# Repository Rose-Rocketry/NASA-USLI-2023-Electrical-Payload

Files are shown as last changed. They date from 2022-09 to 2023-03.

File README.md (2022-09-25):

# NASA-USLI-2023-Electrical-Payload

Welcome!

This repository is still in progress and houses the majority of the camera integration/functionality code for the NASA USLI 2023 Competition

Action items as of 9/25/2022:
- Add modular methods so other parts of the program can be run (i.e. "img2BW" "applySobel")
- Figure out how to do command line prompting to run the program so RF payload can use our program
- Prompt program to run with "[Radio Callsign] B2 A1 C3 D4 ..."
- Pick out and purchase microcontroller and antenna design
- Integrate camera to a microcontroller and upload code to microcontroller to run on boot (similar to systemctl)
- Have RF transmissions dictate the microcontroller operations of when to take pictures and apply filters (to be decided by RF Payload subsystem)
- Build antenna to send RF transmissions
- House camera payload in chassis to be determined by Mechanical Payload Team

Google Jamboard for Camera Payload: https://jamboard.google.com/d/17pDWzvR5QUZo6pmwbOdQxkDinwWt7RJfm15y4S94SMs/viewer?f=0

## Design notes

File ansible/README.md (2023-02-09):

# Local testing with vagrant
> Note: we should try to aim to make this as similar to the real thing as possible, but there's a limit to what we can test without the actual hardware

1. Install vagrant and ansible
> Note: If running on windows, make sure [Hyper-V](https://learn.microsoft.com/en-us/virtualization/hyper-v-on-windows/quick-start/enable-hyper-v) is enabled. This will require admin privliges in the terminal you expect to be working in as a limitation to Hyper-V.
2. Run `vagrant up`
> Note: Rose-Hulman blocks all DNS traffic that isn't to their dns servers, which breaks vagrant. This can be fixed by manually editing `/etc/resolv.conf` with `vagrant ssh`
3. After making changes to the ansible files, run `vagrant provision` to re-apply them. Run `vagrant destroy -f` to delete the VM's, and `vagrant up` to create new ones

# Flight Computer Setup Instructions
0. Required software: Raspberry Pi Imager, ansible
1. Flash "Raspberry Pi OS Lite (32 bit)" to the sd card with the Raspberry Pi Imager. Change the following settings:
```
[X] Set Hotname: rocket-pi
[X] Enable SSH
    [X] Password
    [ ] Public Key
[X] Set username and password
    Username: pi
```
> Note: We're gonna switch to 64-bit when we get the new pi's
2. Copying `wpa_supplicant.conf` from `boot` to the boot partition
> Note: If your using RHIT-OPEN, you must add the MAC address to clearpass before booting the pi
3. Eject the SD and boot the pi. This can take over 5 minutes!
4. Ensure you have ssh access with `ssh pi@rocket-pi`
> If you have a different hostname, be sure to update inventory.txt
5. Setup all of the software with `ansible-playbook playbook.yaml -i ansible_hosts` or `ansible-playbook playbook.yaml -i subscale_hosts` for subscale. This can also take a very long time

# IP Addresses
Withing the xblink network, all devices will be in the `10.82.104.0/24` subnet. The groundstation will have an ip of `10.82.104.2`, and rocket(s) will have ip(s) of `10.82.104.3`, `10.82.104.4`, etc...
> 82.104 is ASCII for `"Rh"`

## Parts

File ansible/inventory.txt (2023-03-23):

rocket-pi ansible_user=pi ansible_host=10.82.104.3 xb_device=/dev/ttyAMA0 xb_ip=10.82.104.3/24

[rocket]
rocket-pi

[pi]
rocket-pi

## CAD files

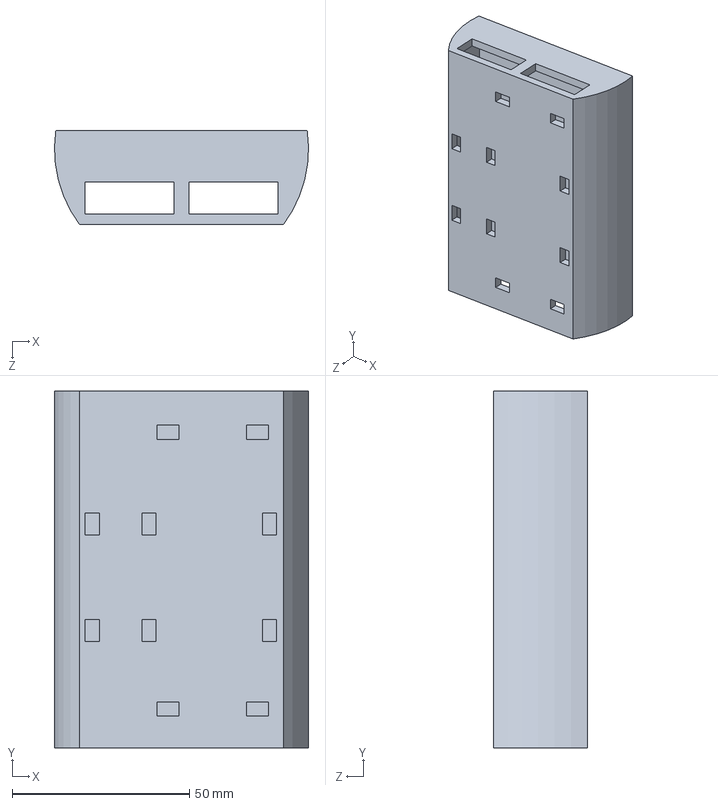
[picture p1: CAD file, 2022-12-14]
CAD/Subscale SDR Extension/Housing.SLDPRT
71.6 x 100.6 x 26.6 mm

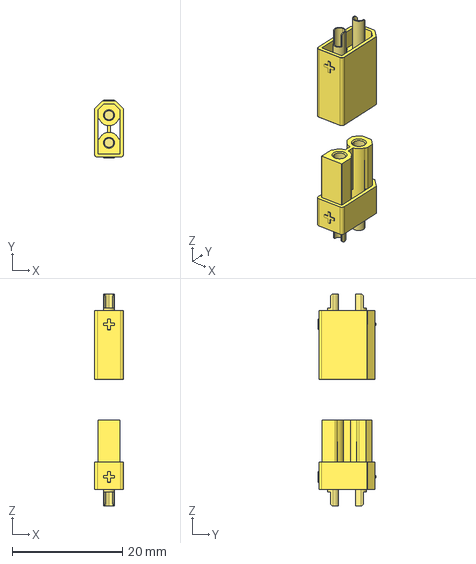
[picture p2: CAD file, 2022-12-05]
Motherboard/motherboard_2022_2023/3d_models/XT30U-M.step
5.25 x 10.4 x 38.5 mm

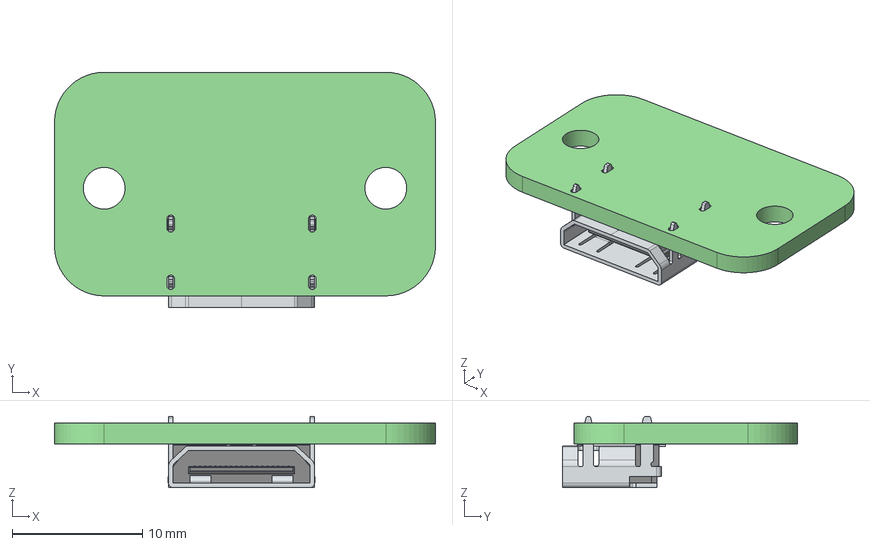
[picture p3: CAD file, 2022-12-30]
Motherboard/motherboard_2022_2023/hdmi_to_csi.step
29.2 x 18.1 x 5.45 mm
hdmi_to_csi PCB

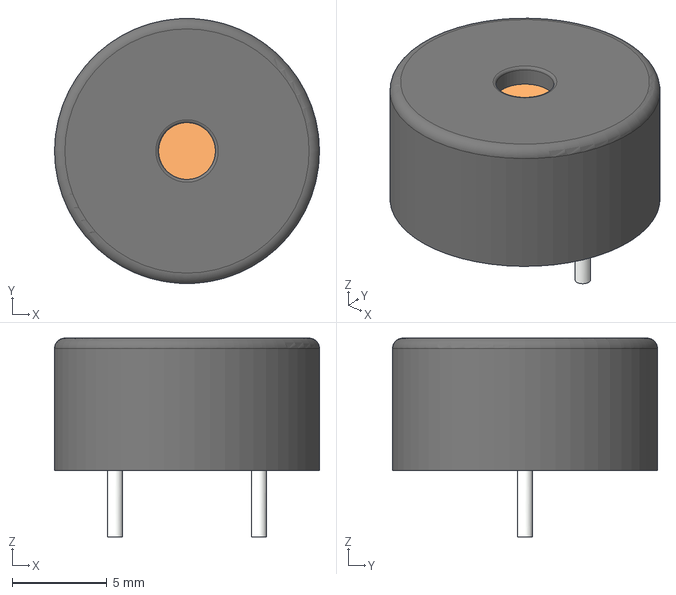
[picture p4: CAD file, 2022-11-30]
Motherboard/motherboard_2022_2023/3d_models/Piezo Buzzer.step
14.0 x 14.0 x 10.5 mm

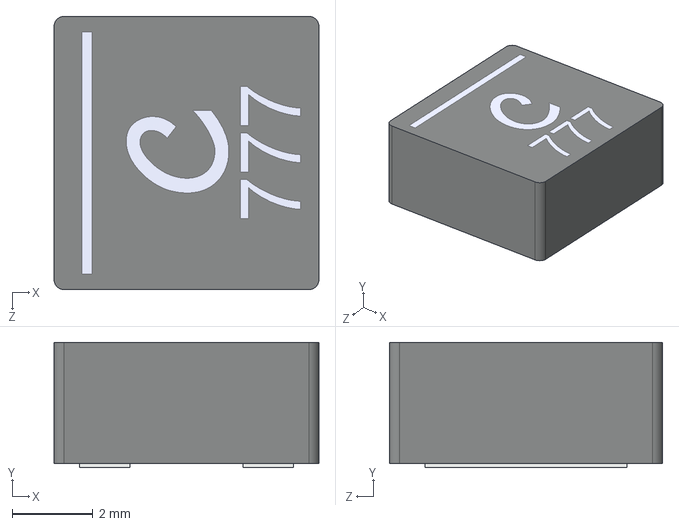
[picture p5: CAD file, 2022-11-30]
Motherboard/motherboard_2022_2023/3d_models/Coilcraft-XAL6030.step
6.56 x 3.10 x 6.76 mm

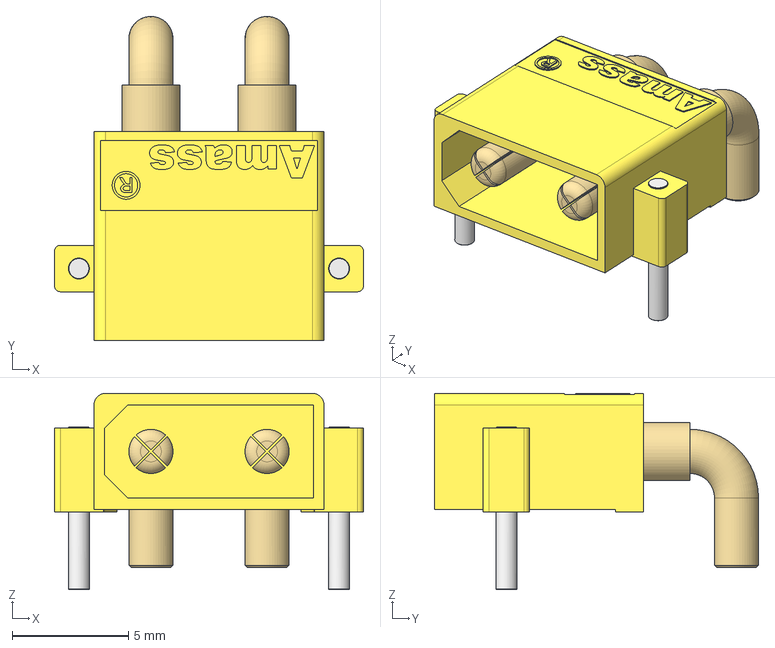
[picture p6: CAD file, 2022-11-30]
Motherboard/motherboard_2022_2023/3d_models/Amass_XT30PW-M.step
13.3 x 13.9 x 8.45 mm

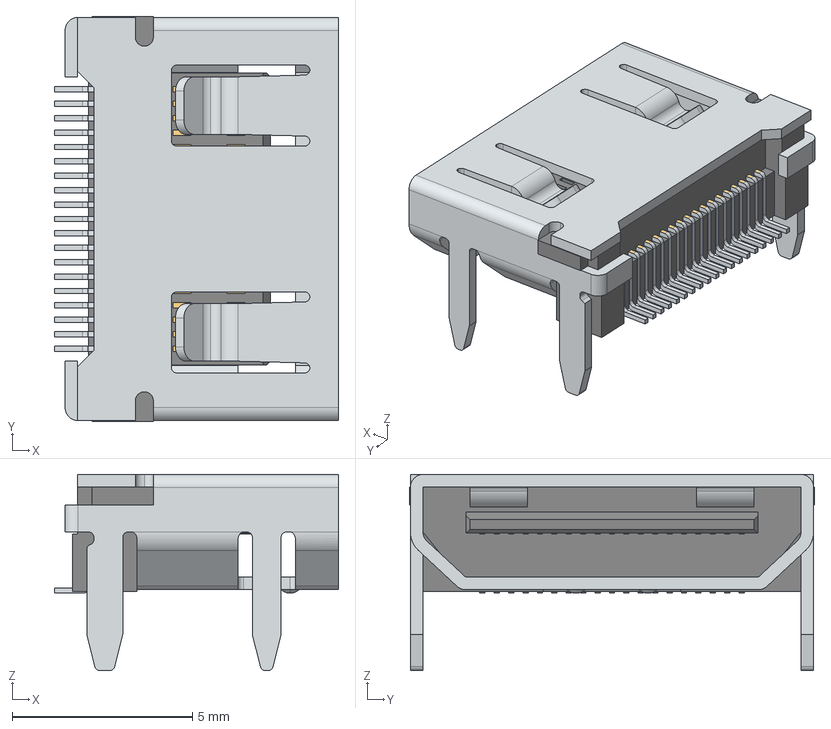
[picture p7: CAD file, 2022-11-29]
Motherboard/motherboard_2022_2023/3d_models/WURTH_685119136923.step
7.90 x 11.2 x 5.45 mm

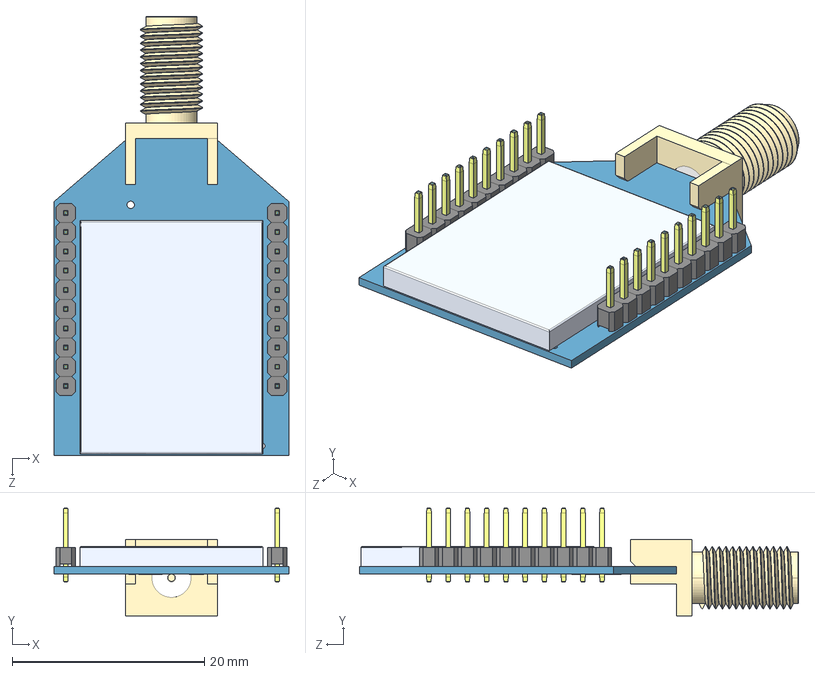
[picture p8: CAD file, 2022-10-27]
Motherboard/motherboard_2022_2023/3d_models/XBProRPSMA.step
24.4 x 11.2 x 45.6 mm
XBP24_board
2mmHeaderPin_straight x 20
XBPro_shield
RPSMA_XBee

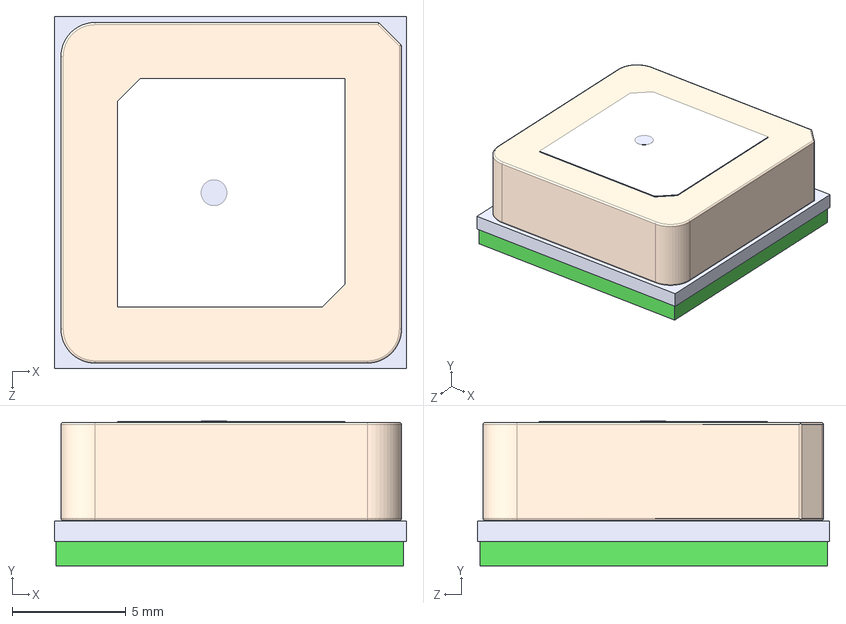
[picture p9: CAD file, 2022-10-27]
Motherboard/motherboard_2022_2023/3d_models/SAM_AP214.STEP
15.5 x 6.38 x 15.5 mm
Sam cavity
SAM PCB
SAM ANT

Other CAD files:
CAD/Subscale SDR Extension/Housing.STL

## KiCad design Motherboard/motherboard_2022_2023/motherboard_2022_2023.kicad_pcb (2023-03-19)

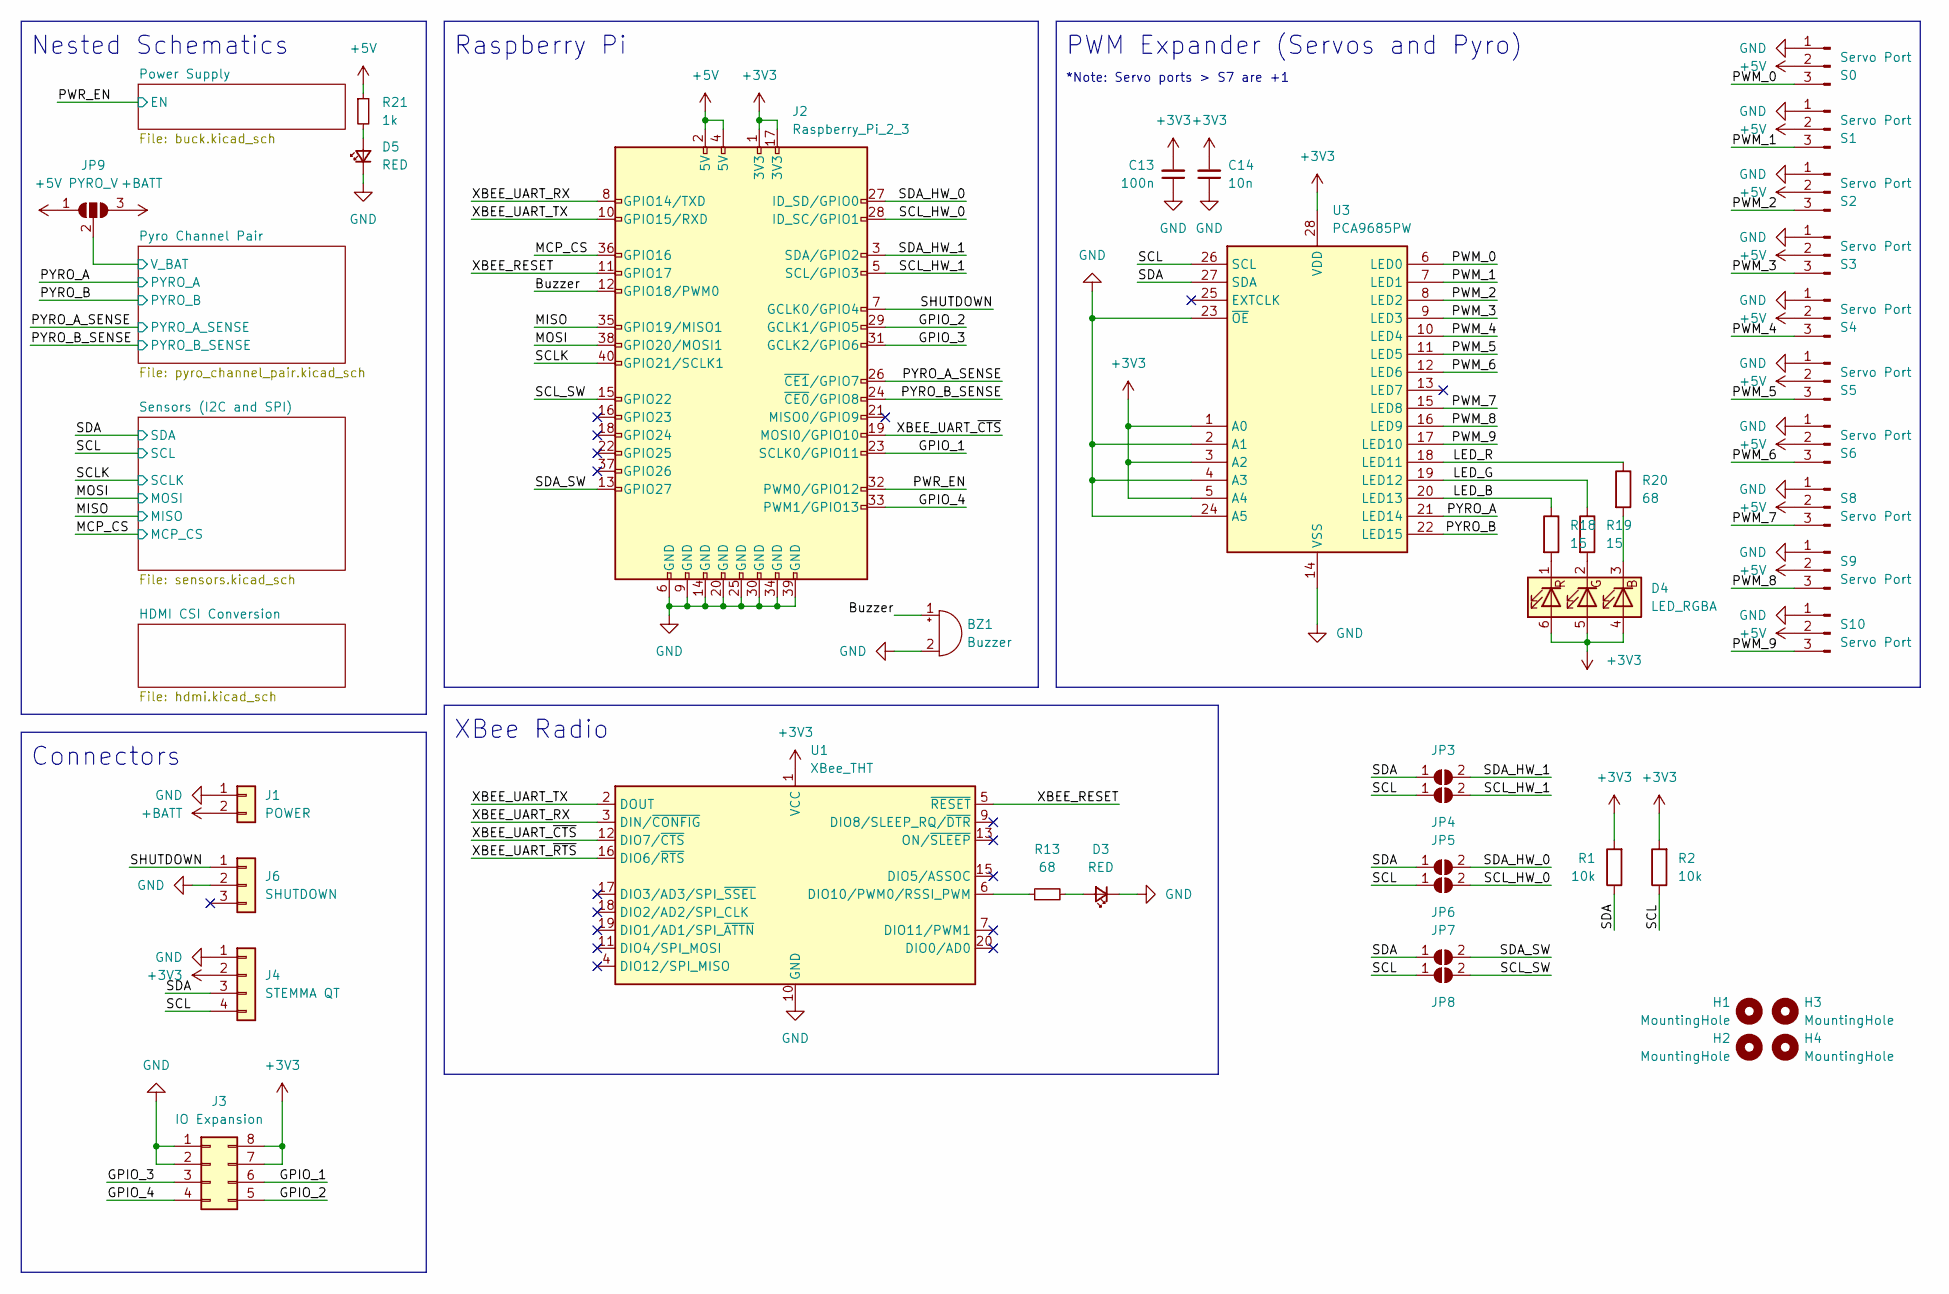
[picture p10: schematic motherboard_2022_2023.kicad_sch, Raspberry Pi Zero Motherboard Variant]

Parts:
BZ1: Buzzer; CPI-1375-80T
C13: 100n; C_0603_1608Metric
C14: 10n; C_0603_1608Metric
D3, D5: RED; LED_0603_1608Metric
D4: LED_RGBA; LED_RGB_5050-6
H1, H2, H3, H4: MountingHole; MountingHole_3.2mm_M3
J1: POWER; AMASS_XT30U-M_1x02_P5.0mm_Vertical
J2: Raspberry_Pi_2_3; PI_Zero
J3: IO Expansion; PinHeader_2x04_P2.54mm_Horizontal
J4: STEMMA QT; JST_SH_SM04B-SRSS-TB_1x04-1MP_P1.00mm_Horizontal
J6: SHUTDOWN; PinHeader_1x03_P2.54mm_Horizontal
JP3, JP4, JP5, JP6, JP7, JP8: SolderJumper_2_Open; SolderJumper-2_P1.3mm_Open_RoundedPad1.0x1.5mm
JP9: PYRO_V; SolderJumper-3_P2.0mm_Open_TrianglePad1.0x1.5mm
R1, R2: 10k; R_0603_1608Metric
R13, R20: 68; R_0603_1608Metric
R18, R19: 15; R_0603_1608Metric
R21: 1k; R_0603_1608Metric
S0, S1, S2, S3, S4, S5, S6, S8, S9, S10: Servo Port; PinHeader_1x03_P2.54mm_Horizontal
U1: XBee_THT; XBee-THT
U3: PCA9685PW; TSSOP-28_4.4x9.7mm_P0.65mm

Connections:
+3V3: C13.2, C14.2, D4.4 (BA), D4.5 (GA), D4.6 (RA), J2.1 (3V3), J2.17 (3V3), J3.7, J3.8, J4.2, R1.2, R2.2, U1.1 (VCC), U3.1 (A0), U3.3 (A2), U3.5 (A4), U3.28 (VDD); also elsewhere on the board
+5V: J2.2 (5V), J2.4 (5V), JP9.1 (A), R21.1, S0.2, S1.2, S2.2, S3.2, S4.2, S5.2, S6.2, S8.2, S9.2, S10.2; also elsewhere on the board
+BATT: J1.2, JP9.3 (B); also elsewhere on the board
/Buzzer: BZ1.1 (-), J2.12 (GPIO18/PWM0)
/GPIO_1: J2.23 (SCLK0/GPIO11), J3.6
/GPIO_2: J2.29 (GCLK1/GPIO5), J3.5
/GPIO_3: J2.31 (GCLK2/GPIO6), J3.3
/GPIO_4: J2.33 (PWM1/GPIO13), J3.4
/LED_B: R20.1, U3.18 (LED11)
/LED_G: R19.1, U3.19 (LED12)
/LED_R: R18.1, U3.20 (LED13)
/MCP_CS: J2.36 (GPIO16); also elsewhere on the board
/MISO: J2.35 (GPIO19/MISO1); also elsewhere on the board
/MOSI: J2.38 (GPIO20/MOSI1); also elsewhere on the board
/PWM_0: S0.3, U3.6 (LED0)
/PWM_1: S1.3, U3.7 (LED1)
/PWM_2: S2.3, U3.8 (LED2)
/PWM_3: S3.3, U3.9 (LED3)
/PWM_4: S4.3, U3.10 (LED4)
/PWM_5: S5.3, U3.11 (LED5)
/PWM_6: S6.3, U3.12 (LED6)
/PWM_7: S8.3, U3.15 (LED8)
/PWM_8: S9.3, U3.16 (LED9)
/PWM_9: S10.3, U3.17 (LED10)
/PWR_EN: J2.32 (PWM0/GPIO12); also elsewhere on the board
/PYRO_A: U3.21 (LED14); also elsewhere on the board
/PYRO_A_SENSE: J2.26 (~CE1/GPIO7); also elsewhere on the board
/PYRO_B: U3.22 (LED15); also elsewhere on the board
/PYRO_B_SENSE: J2.24 (~CE0/GPIO8); also elsewhere on the board
/Pyro Channel Pair/V_BAT: JP9.2 (C); also elsewhere on the board
/SCL: J4.4, JP4.1 (A), JP6.1 (A), JP8.1 (A), R2.1, U3.26 (SCL); also elsewhere on the board
/SCLK: J2.40 (GPIO21/SCLK1); also elsewhere on the board
/SCL_HW_0: J2.28 (ID_SC/GPIO1), JP6.2 (B)
/SCL_HW_1: J2.5 (SCL/GPIO3), JP4.2 (B)
/SCL_SW: J2.15 (GPIO22), JP8.2 (B)
/SDA: J4.3, JP3.1 (A), JP5.1 (A), JP7.1 (A), R1.1, U3.27 (SDA); also elsewhere on the board
/SDA_HW_0: J2.27 (ID_SD/GPIO0), JP5.2 (B)
/SDA_HW_1: J2.3 (SDA/GPIO2), JP3.2 (B)
/SDA_SW: J2.13 (GPIO27), JP7.2 (B)
/SHUTDOWN: J2.7 (GCLK0/GPIO4), J6.1
/XBEE_RESET: J2.11 (GPIO17), U1.5 (~RESET)
/XBEE_UART_RX: J2.8 (GPIO14/TXD), U1.3 (DIN/~CONFIG)
/XBEE_UART_TX: J2.10 (GPIO15/RXD), U1.2 (DOUT)
/XBEE_UART_~CTS: J2.19 (MOSI0/GPIO10), U1.12 (DIO7/~CTS)
/XBEE_UART_~RTS: U1.16 (DIO6/~RTS)
GND: BZ1.2 (+), C13.1, C14.1, D3.1 (K), D5.1 (K), J1.1, J2.6 (GND), J2.9 (GND), J2.14 (GND), J2.20 (GND), J2.25 (GND), J2.30 (GND), J2.34 (GND), J2.39 (GND), J3.1, J3.2, J4.1, J6.2, S0.1, S1.1, S2.1, S3.1, S4.1, S5.1, S6.1, S8.1, S9.1, S10.1, U1.10 (GND), U3.2 (A1), U3.4 (A3), U3.14 (VSS), U3.23 (~OE), U3.24 (A5); also elsewhere on the board
unnamed: D3.2 (A), R13.2
unnamed: D4.1 (RK), R18.2
unnamed: D4.2 (GK), R19.2
unnamed: D4.3 (BK), R20.2
unnamed: D5.2 (A), R21.2
unnamed: R13.1, U1.6 (DIO10/PWM0/RSSI_PWM)

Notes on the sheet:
XBee Radio
Nested Schematics
Raspberry Pi
*Note: Servo ports > S7 are +1
Connectors
PWM Expander (Servos and Pyro)

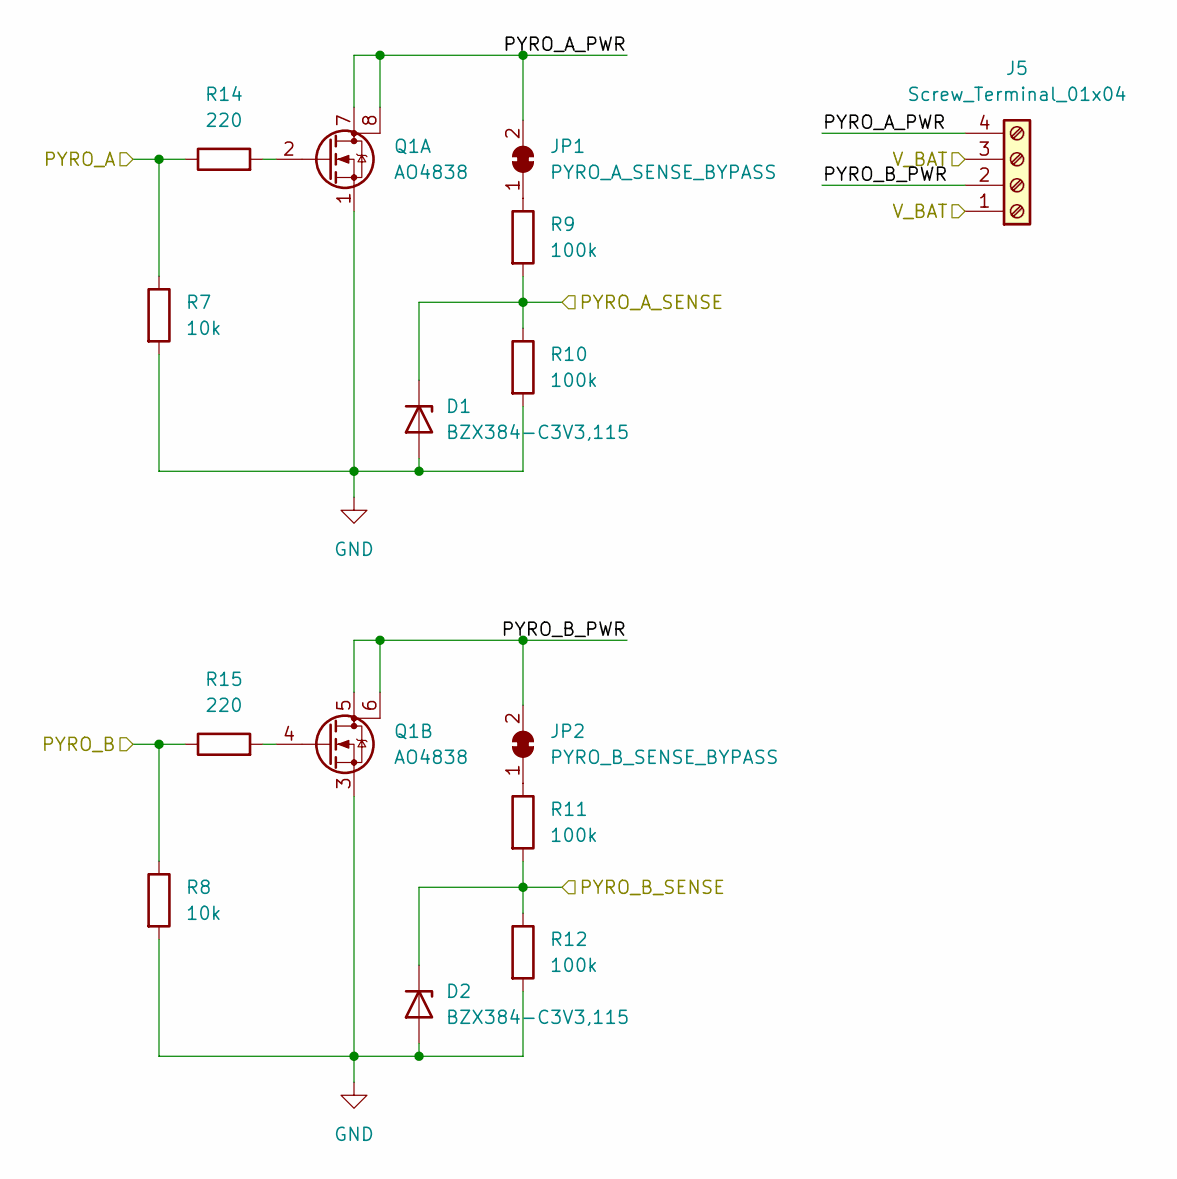
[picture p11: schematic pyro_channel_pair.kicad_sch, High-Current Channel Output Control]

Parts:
D1, D2: BZX384-C3V3,115; D_SOD-323
J5: Screw_Terminal_01x04; TerminalBlock_Phoenix_MPT-0,5-4-2.54_1x04_P2.54mm_Horizontal
JP1: PYRO_A_SENSE_BYPASS; SolderJumper-2_P1.3mm_Bridged_RoundedPad1.0x1.5mm
JP2: PYRO_B_SENSE_BYPASS; SolderJumper-2_P1.3mm_Bridged_RoundedPad1.0x1.5mm
Q1: AO4838; SOIC-8_3.9x4.9mm_P1.27mm
R7, R8: 10k; R_0603_1608Metric
R9, R10, R11, R12: 100k; R_0603_1608Metric
R14, R15: 220; R_0603_1608Metric

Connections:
/PYRO_A: R7.1, R14.1; also elsewhere on the board
/PYRO_A_SENSE: D1.1 (K), R9.2, R10.1; also elsewhere on the board
/PYRO_B: R8.1, R15.1; also elsewhere on the board
/PYRO_B_SENSE: D2.1 (K), R11.2, R12.1; also elsewhere on the board
/Pyro Channel Pair/PYRO_A_PWR: J5.4, JP1.2 (B), Q1.7 (D), Q1.8 (D)
/Pyro Channel Pair/PYRO_B_PWR: J5.2, JP2.2 (B), Q1.5 (D), Q1.6 (D)
/Pyro Channel Pair/V_BAT: J5.1, J5.3; also elsewhere on the board
GND: D1.2 (A), D2.2 (A), Q1.1 (S), Q1.3 (S), R7.2, R8.2, R10.2, R12.2; also elsewhere on the board
unnamed: JP1.1 (A), R9.1
unnamed: JP2.1 (A), R11.1
unnamed: Q1.2 (G), R14.2
unnamed: Q1.4 (G), R15.2

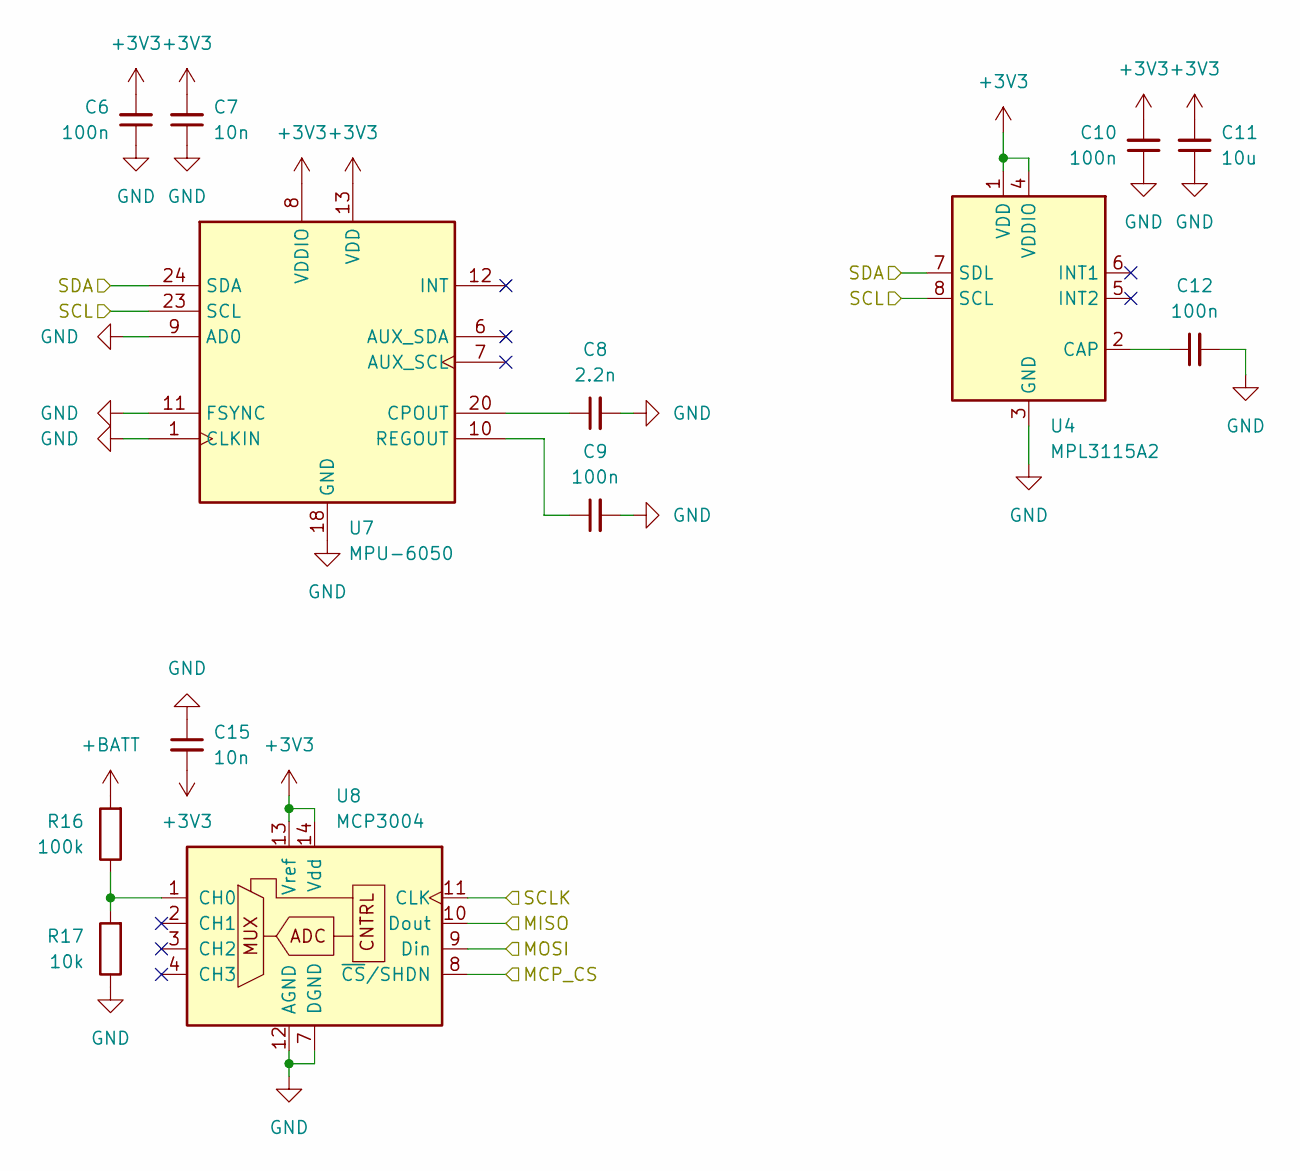
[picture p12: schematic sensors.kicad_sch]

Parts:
C6, C9, C10, C12: 100n; C_0603_1608Metric
C7, C15: 10n; C_0603_1608Metric
C8: 2.2n; C_0603_1608Metric
C11: 10u; C_0603_1608Metric
R16: 100k; R_0603_1608Metric
R17: 10k; R_0603_1608Metric
U4: MPL3115A2; NXP_LGA-8_3x5mm_P1.25mm_H1.1mm
U7: MPU-6050; InvenSense_QFN-24_4x4mm_P0.5mm
U8: MCP3004; SOIC-14_3.9x8.7mm_P1.27mm

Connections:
+3V3: C6.2, C7.2, C10.2, C11.2, C15.2, U4.1 (VDD), U4.4 (VDDIO), U7.8 (VDDIO), U7.13 (VDD), U8.13 (Vref), U8.14 (Vdd); also elsewhere on the board
+BATT: R16.2; also elsewhere on the board
/MCP_CS: U8.8 (~CS/SHDN); also elsewhere on the board
/MISO: U8.10 (Dout); also elsewhere on the board
/MOSI: U8.9 (Din); also elsewhere on the board
/SCL: U4.8 (SCL), U7.23 (SCL); also elsewhere on the board
/SCLK: U8.11 (CLK); also elsewhere on the board
/SDA: U4.7 (SDL), U7.24 (SDA); also elsewhere on the board
GND: C6.1, C7.1, C8.2, C9.2, C10.1, C11.1, C12.2, C15.1, R17.1, U4.3 (GND), U7.1 (CLKIN), U7.9 (AD0), U7.11 (FSYNC), U7.18 (GND), U8.7 (DGND), U8.12 (AGND); also elsewhere on the board
unnamed: C8.1, U7.20 (CPOUT)
unnamed: C9.1, U7.10 (REGOUT)
unnamed: C12.1, U4.2 (CAP)
unnamed: R16.1, R17.2, U8.1 (CH0)

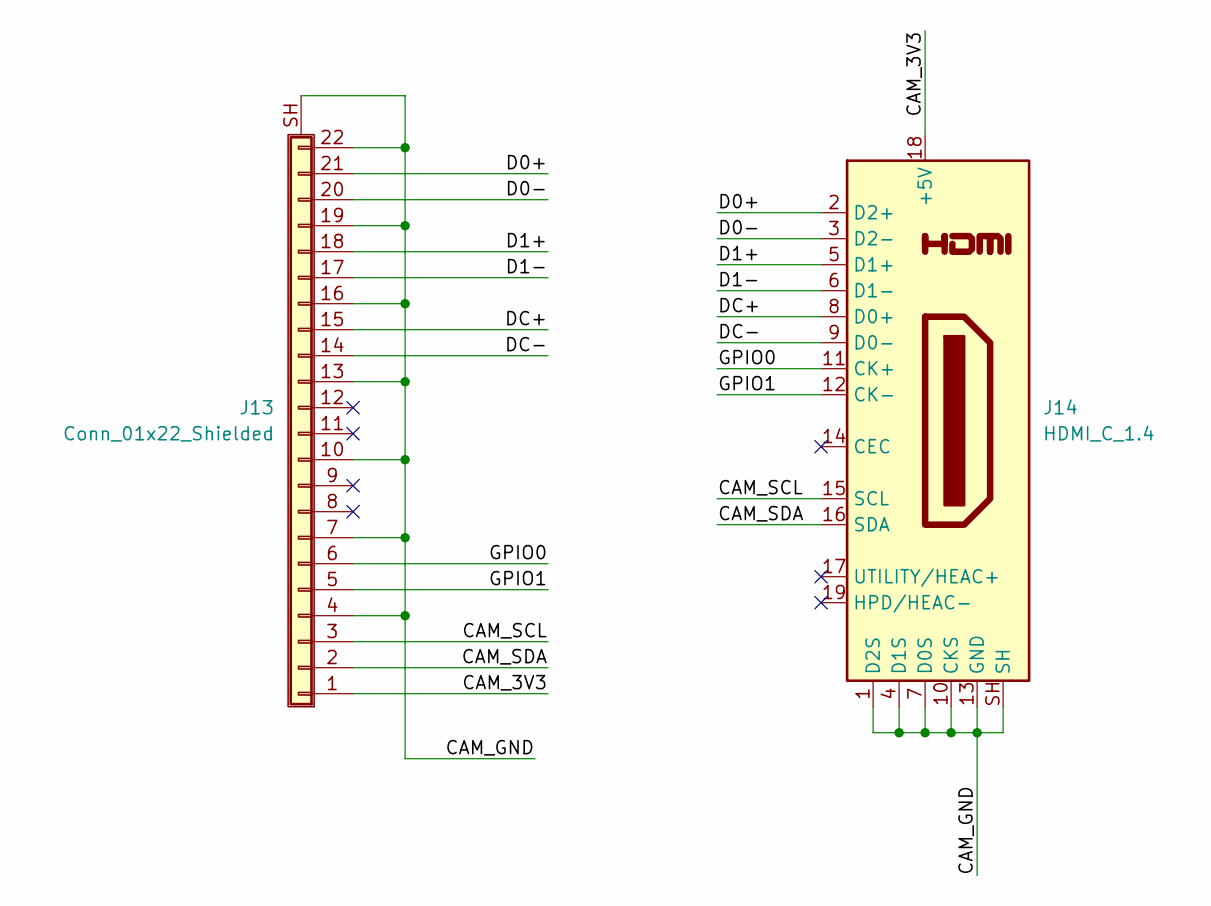
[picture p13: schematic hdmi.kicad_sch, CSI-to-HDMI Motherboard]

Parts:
J13: Conn_01x22_Shielded; MOLEX 22 Pin FPC 54548-2271
J14: HDMI_C_1.4; WURTH_685119136923

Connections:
/HDMI CSI Conversion/CAM_3V3: J13.1, J14.18 (+5V)
/HDMI CSI Conversion/CAM_GND: J13.4, J13.7, J13.10, J13.13, J13.16, J13.19, J13.22, J13.SH (Shield), J14.1 (D2S), J14.4 (D1S), J14.7 (D0S), J14.10 (CKS), J14.13 (GND), J14.SH
/HDMI CSI Conversion/CAM_SCL: J13.3, J14.15 (SCL)
/HDMI CSI Conversion/CAM_SDA: J13.2, J14.16 (SDA)
/HDMI CSI Conversion/D0+: J13.21, J14.2 (D2+)
/HDMI CSI Conversion/D0-: J13.20, J14.3 (D2-)
/HDMI CSI Conversion/D1+: J13.18, J14.5 (D1+)
/HDMI CSI Conversion/D1-: J13.17, J14.6 (D1-)
/HDMI CSI Conversion/DC+: J13.15, J14.8 (D0+)
/HDMI CSI Conversion/DC-: J13.14, J14.9 (D0-)
/HDMI CSI Conversion/GPIO0: J13.6, J14.11 (CK+)
/HDMI CSI Conversion/GPIO1: J13.5, J14.12 (CK-)

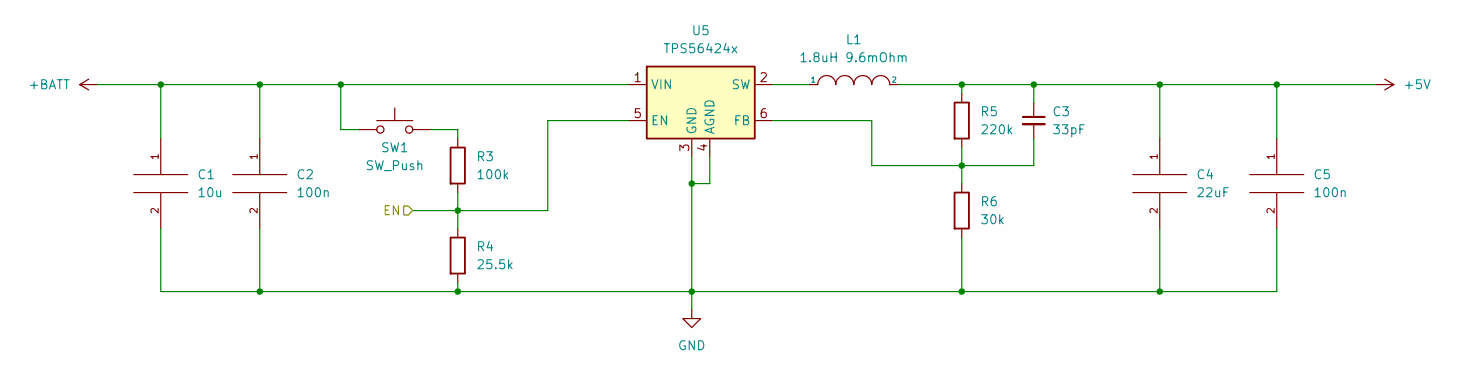
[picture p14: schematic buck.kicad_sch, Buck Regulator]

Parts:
C1: 10u; C_0603_1608Metric
C2, C5: 100n; C_0603_1608Metric
C3: 33pF; C_0603_1608Metric
C4: 22uF; C_0603_1608Metric
L1: 1.8uH 9.6mOhm; L_Coilcraft_XAL60xx_6.36x6.56mm
R3: 100k; R_0603_1608Metric
R4: 25.5k; R_0603_1608Metric
R5: 220k; R_0603_1608Metric
R6: 30k; R_0603_1608Metric
SW1: SW_Push; SW_PUSH_6mm
U5: TPS56424x; SOT-563

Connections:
+5V: C3.1, C4.1, C5.1, L1.2, R5.1; also elsewhere on the board
+BATT: C1.1, C2.1, SW1.1, U5.1 (VIN); also elsewhere on the board
/PWR_EN: R3.2, R4.1, U5.5 (EN); also elsewhere on the board
GND: C1.2, C2.2, C4.2, C5.2, R4.2, R6.2, U5.3 (GND), U5.4 (AGND); also elsewhere on the board
unnamed: C3.2, R5.2, R6.1, U5.6 (FB)
unnamed: L1.1, U5.2 (SW)
unnamed: R3.1, SW1.2

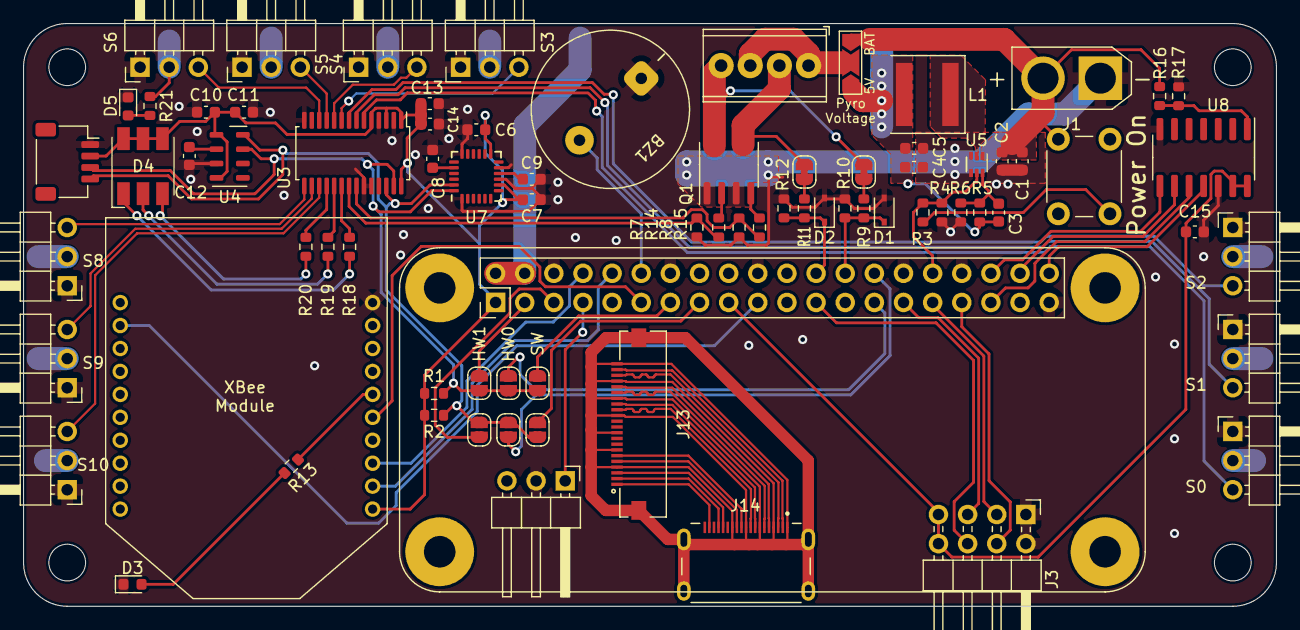
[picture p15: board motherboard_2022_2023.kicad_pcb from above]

Board: 2 copper layers, 109.2 x 50.8 mm, 82 parts (0 on the bottom side), 76 nets.

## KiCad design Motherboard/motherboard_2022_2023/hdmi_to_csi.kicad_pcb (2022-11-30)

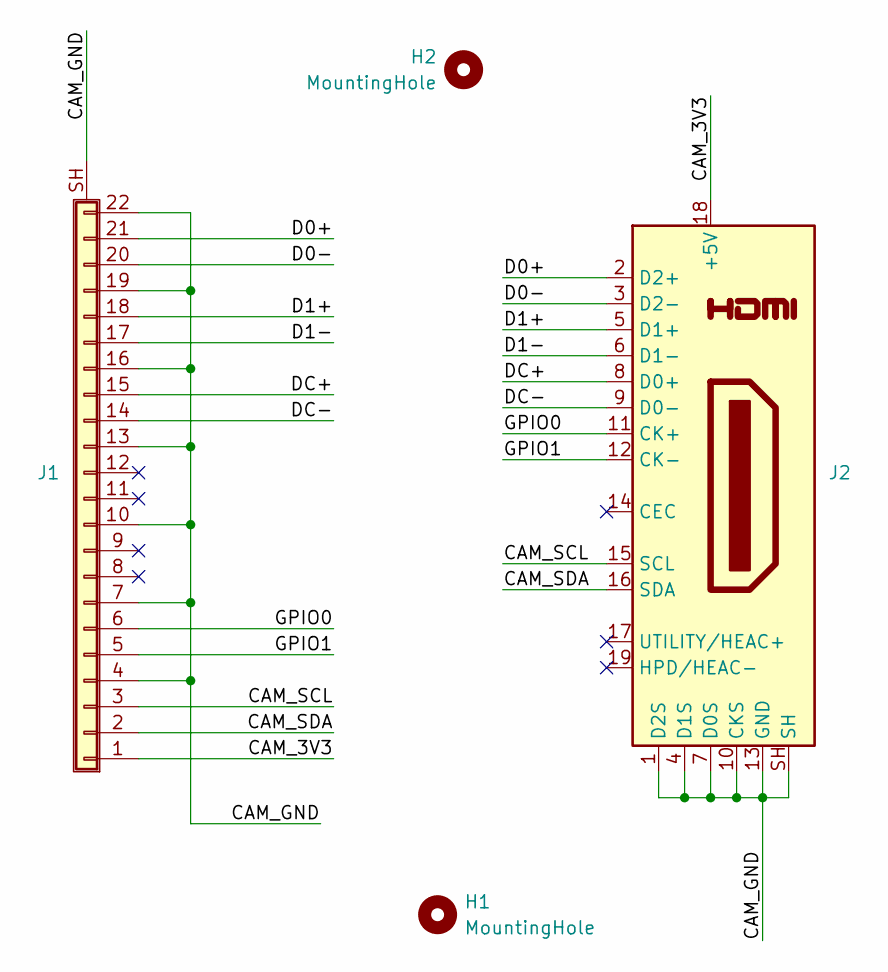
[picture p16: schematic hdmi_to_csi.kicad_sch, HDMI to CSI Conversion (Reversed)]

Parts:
H1, H2: MountingHole; MountingHole_3.2mm_M3
J1: MOLEX 22 Pin FPC 54548-2271
J2: WURTH_685119136923

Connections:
/CAM_3V3: J1.1, J2.18 (+5V)
/CAM_GND: J1.4, J1.7, J1.10, J1.13, J1.16, J1.19, J1.22, J1.SH (Shield), J2.1 (D2S), J2.4 (D1S), J2.7 (D0S), J2.10 (CKS), J2.13 (GND), J2.SH
/CAM_SCL: J1.3, J2.15 (SCL)
/CAM_SDA: J1.2, J2.16 (SDA)
/D0+: J1.21, J2.2 (D2+)
/D0-: J1.20, J2.3 (D2-)
/D1+: J1.18, J2.5 (D1+)
/D1-: J1.17, J2.6 (D1-)
/DC+: J1.15, J2.8 (D0+)
/DC-: J1.14, J2.9 (D0-)
/GPIO0: J1.6, J2.11 (CK+)
/GPIO1: J1.5, J2.12 (CK-)

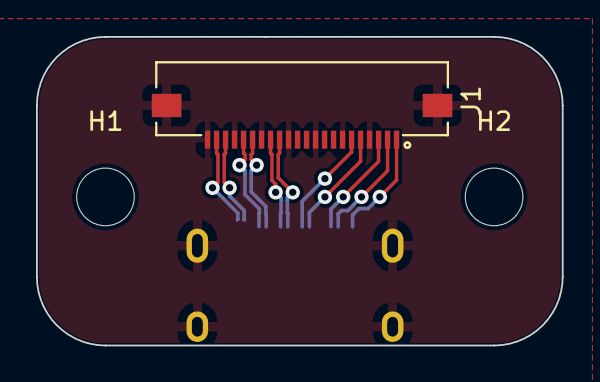
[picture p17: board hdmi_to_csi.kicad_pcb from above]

Board: 2 copper layers, 29.2 x 17.1 mm, 4 parts (1 on the bottom side), 12 nets.

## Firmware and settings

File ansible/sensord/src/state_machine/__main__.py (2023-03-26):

import json
import paho.mqtt.client as mqtt
import logging
import enum
import math
import os
from . import state_machine, vector
from .pwm_device import Servo, ServoGroup, PWMPort
from .parser import parse_aprs_commands
from typing import Callable, Optional
from collections import deque
from numbers import Number

logging.basicConfig(level=logging.INFO)

with open("/opt/git_status") as f:
    GIT_STATUS = f.read()

TOPIC_PREFIX = "sensors/"
TOPIC_STATE_CURRENT = "state_machine/state/current"
TOPIC_STATE_ALL = "state_machine/state/all"
TOPIC_STATE_SET = "state_machine/state/set"
MIN_UPDATE_RATE = 20

class States(enum.IntEnum):
    SETUP_OPEN_DOOR_HOLD = enum.auto()
    SETUP_OPEN_CLOSE_DOOR = enum.auto()
    SETUP_CLOSE_DOOR = enum.auto()
    SETUP_CHUTE_OPEN = enum.auto()
    SETUP_CHUTE_CLOSE = enum.auto()
    LAUNCHPAD = enum.auto()
    FLYING = enum.auto()
    DEPLOY_CHUTE = enum.auto()
    DEPLOY_CHUTE_WAIT = enum.auto()
    DEPLOY_LEGS = enum.auto()
    DEPLOY_LEGS_WAIT = enum.auto()
    ORIENT = enum.auto()
    DEPLOY_DOOR = enum.auto()
    DEPLOY_DOOR_WAIT = enum.auto()
    DEPLOY_ARM = enum.auto()
    DEPLOY_ARM_WAIT = enum.auto()
    APRS_LISTEN = enum.auto()
    EXECUTE_COMMANDS = enum.auto()
    DONE = enum.auto()
    KILL = enum.auto()
    SHUTDOWN = enum.auto()


# Launch and Landing Detection
LAUNCH_DETECT_ALTITUDE_DELTA = 500
FLYING_MIN_DURATION = 3 * 60
FLYING_STABLE_DURATION = 60
FLYING_STABLE_GAP_DURATION = 2
FLYING_STABLE_MAX_SPEED = 2

# Self-orientation
VECTOR_DOWN = (-1, 0, 0)
VECTOR_SIDE = (0, 0, 1)
ORIENT_SERVO = ServoGroup(Servo(4), Servo(10, inverted=True))
ORIENT_P = 0.5
ORIENT_K = 0.6
ORIENT_THRESHOLD = math.radians(5)
ORIENT_TIMEOUT = 8
ORIENT_LOCKOUT = math.radians(50)

# Deployment
DEPLOY_CHUTE_SERVO = Servo(8)
DEPLOY_CHUTE_ANGLE_OPEN = -90
DEPLOY_CHUTE_ANGLE_CLOSE = 90
DEPLOY_CHUTE_DURATION = 3
DEPLOY_CHUTE_WAIT = 3
DEPLOY_LEGS_CHANNEL_A = PWMPort(14)
DEPLOY_LEGS_CHANNEL_B = PWMPort(15)
DEPLOY_LEGS_POWER = 0.5
DEPLOY_LEGS_DURATION = 5  # On time of burn wire
DEPLOY_LEGS_WAIT = 5  # How long to wait after deploying to start orienting
DEPLOY_DOOR_SERVO = ServoGroup(Servo(9), Servo(5))
DEPLOY_DOOR_POWER = 1
DEPLOY_DOOR_DURATION = 3
DEPLOY_DOOR_WAIT = 2
DEPLOY_ARM_SERVO = Servo(6)
DEPLOY_ARM_ANGLE_STOW = 90
DEPLOY_ARM_ANGLE_DEPLOY = -15
DEPLOY_ARM_DURATION = 4
DEPLOY_ARM_WAIT = 2

# APRS
APRS_CALLSIGN = "KQ4CTL"


CLOSE_ON_EXIT = [
    DEPLOY_CHUTE_SERVO,
    ORIENT_SERVO,
    DEPLOY_LEGS_CHANNEL_A,
    DEPLOY_LEGS_CHANNEL_B,
    DEPLOY_DOOR_SERVO,
    DEPLOY_ARM_SERVO
]


class RocketStateMachine(state_machine.StateMachine):
    initial_alt: Number
    stable_since: Number
    stable_deque: deque[state_machine.EventAltitude]
    emit_state_change: Callable[[States], None]
    last_received_commands: Optional[list[str]]

    def __init__(self) -> None:
        super().__init__(MIN_UPDATE_RATE)

        self.initial_alt = None
        self.stable_since = None
        self.stable_deque = None
        self.emit_state_change = None
        self.last_received_commands = None

    def handle_event_impl(self, event: state_machine.Event):
        state = self.get_state()

        if isinstance(event, state_machine.EventStateChange):
            self.emit_state_change(state)

        if state == States.SETUP_OPEN_DOOR_HOLD or state == States.SETUP_OPEN_CLOSE_DOOR:
            if isinstance(event, state_machine.EventStateChange):
                self.logger.info(f"Setup: Opening Door")
                DEPLOY_DOOR_SERVO.set_power(DEPLOY_DOOR_POWER)

            if self.last_state_change_elapsed > 5:
                if state == States.SETUP_OPEN_DOOR_HOLD:
                    DEPLOY_DOOR_SERVO.stop()
                    self.set_state(States.DONE)
                else:
                    self.set_state(States.SETUP_CLOSE_DOOR)

        elif state == States.SETUP_CLOSE_DOOR:
            if isinstance(event, state_machine.EventStateChange):
                self.logger.info(f"Setup: Closing Door")
                DEPLOY_DOOR_SERVO.set_power(-DEPLOY_DOOR_POWER)

            if self.last_state_change_elapsed > 0.5:
                DEPLOY_DOOR_SERVO.stop()
                self.set_state(States.DONE)

        elif state == States.SETUP_CHUTE_OPEN:
            if isinstance(event, state_machine.EventStateChange):
                self.logger.info(f"Setup: Opening Chute")
                DEPLOY_CHUTE_SERVO.set_power(DEPLOY_CHUTE_ANGLE_OPEN)

            if self.last_state_change_elapsed > DEPLOY_CHUTE_DURATION:
                DEPLOY_CHUTE_SERVO.stop()
                self.set_state(States.DONE)

        elif state == States.SETUP_CHUTE_CLOSE:
            if isinstance(event, state_machine.EventStateChange):
                self.logger.info(f"Setup: Closing Chute")
                DEPLOY_CHUTE_SERVO.set_power(DEPLOY_CHUTE_ANGLE_CLOSE)

            if self.last_state_change_elapsed > DEPLOY_CHUTE_DURATION:
                DEPLOY_CHUTE_SERVO.stop()
                self.set_state(States.DONE)

        elif state == States.SETUP_CLOSE_DOOR:
            if isinstance(event, state_machine.EventStateChange):
                self.logger.info(f"Closing Door")
                DEPLOY_DOOR_SERVO.set_power(-DEPLOY_DOOR_POWER)

            if self.last_state_change_elapsed > 0.5:
                DEPLOY_DOOR_SERVO.stop()
                self.set_state(States.DONE)

        elif state == States.LAUNCHPAD:
            """
                Waiting on launch pad.
                Listens to altimeter for a rise in 500m (is it meters?)
                Next State: FLYING
                Prev State: None.
            """
            if isinstance(event, state_machine.EventStateChange):
                self.logger.info("Waiting for launch")

            if isinstance(event, state_machine.EventAltitude):
                if self.initial_alt == None:
                    self.initial_alt = event.altitude

                if event.altitude > (self.initial_alt + LAUNCH_DETECT_ALTITUDE_DELTA):
                    self.logger.info(f"Launch detected at t={event.timestamp}, altitude={event.altitude}, initial_alt={self.initial_alt}")
                    self.set_state(States.FLYING)

        elif state == States.FLYING:
            """
                In-Flight state.
                Listens to altimeter for a rise in 500m (is it meters?)
                Next State: DEPLOY_LEGS
                Prev State: None.
            """
            if isinstance(event, state_machine.EventStateChange):
                self.logger.info("Waiting for landing")
                self.stable_since = None
                self.stable_deque = deque()

            if isinstance(event, state_machine.EventAltitude):
                self.stable_deque.append(event)
                
                if event.timestamp - self.stable_deque[0].timestamp <= FLYING_STABLE_GAP_DURATION:
                    return
                
                last_event = self.stable_deque.popleft()

                rate_of_change = (event.altitude - last_event.altitude) / (event.timestamp - last_event.timestamp)

                if abs(rate_of_change) < FLYING_STABLE_MAX_SPEED:
                    if self.stable_since == None:
                        # We are now stable, start the timer
                        self.stable_since = event.timestamp
                else:
                    # We're not stable, reset the timer
                    self.stable_since = None

                # Are we stable and have we been stable long enough?
                stable = (
                    self.stable_since != None
                    and event.timestamp - self.stable_since > FLYING_STABLE_DURATION
                )
                min_time_passed = (
                    self.last_state_change_elapsed > FLYING_MIN_DURATION
                )

                if stable and min_time_passed:
                    self.logger.info(f"Landing detected at t={event.timestamp}, rate_of_change={rate_of_change}")
                    self.get_state(States.DEPLOY_CHUTE)

        elif state == States.DEPLOY_CHUTE:
            if isinstance(event, state_machine.EventStateChange):
                self.logger.info("Deploying chute")
                DEPLOY_CHUTE_SERVO.set_angle(DEPLOY_CHUTE_ANGLE_OPEN)

            if self.last_state_change_elapsed > DEPLOY_CHUTE_DURATION:
                DEPLOY_CHUTE_SERVO.stop()
                self.set_state(States.DEPLOY_CHUTE_WAIT)

        elif state == States.DEPLOY_CHUTE_WAIT:
            if self.last_state_change_elapsed > DEPLOY_CHUTE_WAIT:
                self.set_state(States.DEPLOY_LEGS)

        elif state == States.DEPLOY_LEGS:
            if isinstance(event, state_machine.EventStateChange):
                self.logger.info("Deploying legs")
                DEPLOY_LEGS_CHANNEL_A.set_on_frac(DEPLOY_LEGS_POWER)
                DEPLOY_LEGS_CHANNEL_B.set_on_frac(DEPLOY_LEGS_POWER)

            if self.last_state_change_elapsed > DEPLOY_LEGS_DURATION:
                DEPLOY_LEGS_CHANNEL_A.set_on_frac(0)
                DEPLOY_LEGS_CHANNEL_B.set_on_frac(0)
                self.set_state(States.DEPLOY_LEGS_WAIT)

        elif state == States.DEPLOY_LEGS_WAIT:
            if self.last_state_change_elapsed > DEPLOY_LEGS_WAIT:
                self.set_state(States.ORIENT)

        elif state == States.ORIENT:
                if isinstance(event, state_machine.EventIMU):
                    angle = vector.get_angle(event.gravity, VECTOR_DOWN, VECTOR_SIDE)
                    if self.last_state_change_elapsed > ORIENT_TIMEOUT:
                        if abs(angle) > ORIENT_LOCKOUT:
                            ORIENT_SERVO.stop()
                            self.logger.error("Orient lockout violated, aborting mission")
                            self.set_state(States.DONE)
                        else:
                            ORIENT_SERVO.stop()
                            self.logger.error("Orient timed out, continuing")
                            self.set_state(States.DEPLOY_DOOR)
                    elif abs(angle) > ORIENT_THRESHOLD:
                        power = angle * ORIENT_P + math.copysign(
                            ORIENT_K, angle
                        )
                        self.logger.info(f"Orient angle={angle}, power={power}")
                        ORIENT_SERVO.set_power(power)
                    else:
                        ORIENT_SERVO.stop()
                        self.logger.error("Orient succeeded")
                        self.set_state(States.DEPLOY_DOOR)
                    
        elif state == States.DEPLOY_DOOR:
            if isinstance(event, state_machine.EventStateChange):
                self.logger.info(f"Deploying Door")
                DEPLOY_DOOR_SERVO.set_power(DEPLOY_DOOR_POWER)

            if self.last_state_change_elapsed > DEPLOY_DOOR_DURATION:
                DEPLOY_DOOR_SERVO.stop()
                self.set_state(States.DEPLOY_DOOR_WAIT)

        elif state == States.DEPLOY_DOOR_WAIT:
            if self.last_state_change_elapsed > DEPLOY_DOOR_WAIT:
                self.set_state(States.DEPLOY_ARM)

        elif state == States.DEPLOY_ARM:
            if isinstance(event, state_machine.EventStateChange):
                self.logger.info(f"Deploying Arm")
            
            progress = min(1, self.last_state_change_elapsed / DEPLOY_ARM_DURATION)

            DEPLOY_ARM_SERVO.set_angle((1-progress) * DEPLOY_ARM_ANGLE_STOW + progress * DEPLOY_ARM_ANGLE_DEPLOY)

            if self.last_state_change_elapsed > DEPLOY_ARM_DURATION:
                self.set_state(States.DEPLOY_ARM_WAIT)

        elif state == States.DEPLOY_ARM_WAIT:
            if isinstance(event, state_machine.EventStateChange):
                DEPLOY_ARM_SERVO.set_angle(DEPLOY_ARM_ANGLE_DEPLOY)

            if self.last_state_change_elapsed > DEPLOY_ARM_WAIT:
                DEPLOY_ARM_SERVO.stop()
                self.set_state(States.APRS_LISTEN)

        elif state == States.APRS_LISTEN:
            if not isinstance(event, state_machine.EventAPRSPacket):
                return
            
            self.logger.info(f"APRS Packet received: {event.source}>{event.dest}:{event.info}")

            if event.dest != APRS_CALLSIGN:
                self.logger.warn(f"APRS packet not for {APRS_CALLSIGN}, ignoring")
                return
            
            try:
                commands = parse_aprs_commands(event.info)

                if len(commands) > 0:
                    if self.last_received_commands != None:
                        if self.last_received_commands == commands:
                            self.logger.info("Two matching packets received, executing")
                            self.set_state(States.EXECUTE_COMMANDS)
                        else:
                            self.logger.warn("Two packets had differing commands, ignoring")
                else:
                    self.logger.error("No valid commands found in APRS packet")
                
                self.last_received_commands = commands
            except Exception as e:
                self.logger.error("Error parsing APRS packet", exc_info=e)
        
        elif state == States.EXECUTE_COMMANDS:
            self.logger.info(f"Executing commands {self.last_received_commands}")

            # TODO: Actually execute the commands

            self.set_state(States.DONE)

        elif state == States.DONE:
            pass

        elif state == States.KILL:
            raise InterruptedError("Kill requested")

        elif state == States.SHUTDOWN:
            os.system("shutdown now")
            raise InterruptedError("Shutdown requested")

        else:
            raise RuntimeError(f"Unknown State {state}")


def on_mqtt_connect(client: mqtt.Client, _, flags, rc):
    client.subscribe(TOPIC_PREFIX + "mpl3115", qos=0)
    client.subscribe(TOPIC_PREFIX + "bno055", qos=0)
    client.subscribe(TOPIC_STATE_SET)


def on_mqtt_message(client: mqtt.Client, sm: RocketStateMachine, message: mqtt.MQTTMessage):
    if message.topic == TOPIC_STATE_SET:
        state = States(int(message.payload))
        logging.info(f"Got request to switch to state {state}")
        sm.set_state(state)
    elif message.topic.startswith(TOPIC_PREFIX):
        id = message.topic.removeprefix(TOPIC_PREFIX)
        decoded = json.loads(message.payload)
        if "data" in decoded:
            data = decoded["data"]
            if id == "mpl3115":
                sm.handle_event(state_machine.EventAltitude(data))
            elif id == "bno055":
                sm.handle_event(state_machine.EventIMU(data))
            elif id == "aprs_packets":
                sm.handle_event(state_machine.EventAPRSPacket(data))

if __name__ == "__main__":
    print("State machine is starting")
    print("git status: " + GIT_STATUS)

    try:
        sm = RocketStateMachine()

        def emit_state_change(state):
            client.publish(TOPIC_STATE_CURRENT, int(state), retain=True)

        sm.emit_state_change = emit_state_change

        client = mqtt.Client("state-machine", clean_session=True, userdata=sm)
        client.on_connect = on_mqtt_connect
        client.on_message = on_mqtt_message
        client.enable_logger()
        client.connect("127.0.0.1")
        client.loop_start()

        client.publish(TOPIC_STATE_ALL, "\n".join((repr(a) for a in list(States))), retain=True)

        sm.run(States.LAUNCHPAD)
    finally:
        for pwm_device in CLOSE_ON_EXIT:
            try:
                pwm_device.close()
            except Exception as e:
                print(f"Error closing pwm device {pwm_device.path}: {e}")

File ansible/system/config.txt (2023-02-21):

# For more options and information see
# http://rpf.io/configtxt
# Some settings may impact device functionality. See link above for details

# uncomment if you get no picture on HDMI for a default "safe" mode
#hdmi_safe=1

# uncomment the following to adjust overscan. Use positive numbers if console
# goes off screen, and negative if there is too much border
#overscan_left=16
#overscan_right=16
#overscan_top=16
#overscan_bottom=16

# uncomment to force a console size. By default it will be display's size minus
# overscan.
#framebuffer_width=1280
#framebuffer_height=720

# uncomment if hdmi display is not detected and composite is being output
#hdmi_force_hotplug=1

# uncomment to force a specific HDMI mode (this will force VGA)
#hdmi_group=1
#hdmi_mode=1

# uncomment to force a HDMI mode rather than DVI. This can make audio work in
# DMT (computer monitor) modes
#hdmi_drive=2

# uncomment to increase signal to HDMI, if you have interference, blanking, or
# no display
#config_hdmi_boost=4

# uncomment for composite PAL
#sdtv_mode=2

#uncomment to overclock the arm. 700 MHz is the default.
#arm_freq=800

# Uncomment some or all of these to enable the optional hardware interfaces
#dtparam=i2c_arm=on
#dtparam=i2s=on
#dtparam=spi=on

# Uncomment this to enable infrared communication.
#dtoverlay=gpio-ir,gpio_pin=17
#dtoverlay=gpio-ir-tx,gpio_pin=18

# Additional overlays and parameters are documented /boot/overlays/README

# Enable audio (loads snd_bcm2835)
dtparam=audio=on

# Automatically load overlays for detected cameras
camera_auto_detect=1

# Automatically load overlays for detected DSI displays
display_auto_detect=1

# Enable DRM VC4 V3D driver
dtoverlay=vc4-kms-v3d
max_framebuffers=2

# Disable compensation for displays with overscan
disable_overscan=1

[cm4]
# Enable host mode on the 2711 built-in XHCI USB controller.
# This line should be removed if the legacy DWC2 controller is required
# (e.g. for USB device mode) or if USB support is not required.
otg_mode=1

[all]

[pi4]
# Run as fast as firmware / board allows
arm_boost=1

[all]
# Enable GPIO shutdown
dtoverlay=gpio-shutdown:gpio_pin=4,debounce=5000

# Enable buck converter
gpio=12=op,dh
dtoverlay=gpio-poweroff:gpiopin=12,active_low=1

# Configure pyro sense pins
gpio=7=ip,pn
gpio=8=ip,pn

# Custom DT
dtoverlay=motherboard
dtparam=i2c_gpio_sda=27
dtparam=i2c_gpio_scl=22
dtparam=i2c_gpio_delay_us=2
dtparam=i2c_bus=3
dtparam=i2c_exp_gpio_sda=11
dtparam=i2c_exp_gpio_scl=13
dtparam=i2c_exp_gpio_delay_us=5
dtparam=i2c_exp_bus=4
dtparam=pca_addr=0x55

# Disable bluetooth
# This allows us to use the PL011 for the XBee instead
dtoverlay=disable-bt

# Enable UART
enable_uart=1

# TODO: Enable CTS


# SPI Peripherals
dtparam=spi=on
dtoverlay=spi1-1cs:cs0_pin=16
dtoverlay=mcp3008:spi1-0-present

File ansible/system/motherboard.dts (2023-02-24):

// Definitions for NXP PCA9685A I2C PWM controller on ARM I2C bus.
/dts-v1/;
/plugin/;

/{
	compatible = "brcm,bcm2835";

	fragment@0 {
		target-path = "/";

		__overlay__ {
			i2c_gpio: i2c@0 {
				reg = <0xffffffff>;
				compatible = "i2c-gpio";
				// Value 0x06 is (GPIO_ACTIVE_HIGH|GPIO_OPEN_DRAIN), taken from decompiled dtbo file
				gpios = <&gpio 23 0x06 /* sda */
					 			 &gpio 24 0x06 /* scl */
					>;
				i2c-gpio,delay-us = <2>;
				#address-cells = <1>;
				#size-cells = <0>;
			};
		};
	};

	fragment@1 {
		target-path = "/aliases";
		__overlay__ {
			i2c_gpio = "/i2c@0";
		};
	};

	fragment@2 {
		target-path = "/__symbols__";
		__overlay__ {
			i2c_gpio = "/i2c@0";
		};
	};

	fragment@3 {
		target = <&i2c_gpio>;
		__overlay__ {
			#address-cells = <1>;
			#size-cells = <0>;
			status = "okay";

			pca: pca@40 {
				compatible = "nxp,pca9685-pwm";
				#pwm-cells = <2>;
				// #gpio-cells = <2>;
				reg = <0x40>;
				status = "okay";
			};
		};
	};

	fragment@4 {
		target-path = "/";
		__overlay__ {
			status_leds: leds@0 {
				compatible = "pwm-leds";
				status = "okay";

				led_g: led_g {
					label = "led_g";
					pwms = <&pca 11 20000000>;
					max-brightness = <255>;
					active-low = <1>;
				};

				led_r: led_r {
					label = "led_r";
					pwms = <&pca 12 20000000>;
					max-brightness = <255>;
					active-low = <1>;
				};

				led_b: led_b {
					label = "led_b";
					pwms = <&pca 13 20000000>;
					max-brightness = <255>;
					active-low = <1>;
				};
			};
		};
	};

	fragment@5 {
		target = <&i2c_gpio>;

		__overlay__ {
			#address-cells = <1>;
			#size-cells = <0>;
			status = "okay";
			clock-frequency = <400000>;

			mpu6050: mpu6050@68 {
				compatible = "invensense,mpu6050";
				reg = <0x68>;
				// interrupt-parent = <&gpio>;
				// interrupts = <4 2>;
			};
		};
	};


	fragment@6 {
		target-path = "/";

		__overlay__ {
			i2c_gpio_exp: i2c@4 {
				reg = <0xffffffff>;
				compatible = "i2c-gpio";
				// Value 0x06 is (GPIO_ACTIVE_HIGH|GPIO_OPEN_DRAIN), taken from decompiled dtbo file
				gpios = <&gpio 23 0x06 /* sda */
					 			 &gpio 24 0x06 /* scl */
					>;
				i2c-gpio,delay-us = <2>;
				#address-cells = <1>;
				#size-cells = <0>;
			};
		};
	};

	fragment@7 {
		target-path = "/aliases";
		__overlay__ {
			i2c_gpio_exp = "/i2c@4";
		};
	};

	fragment@8 {
		target-path = "/__symbols__";
		__overlay__ {
			i2c_gpio_exp = "/i2c@4";
		};
	};

	__overrides__ {
		i2c_gpio_sda = <&i2c_gpio>,"gpios:4";
		i2c_gpio_scl = <&i2c_gpio>,"gpios:16";
		i2c_gpio_delay_us = <&i2c_gpio>,"i2c-gpio,delay-us:0";
		i2c_bus = <&i2c_gpio>, "reg:0";

		i2c_exp_gpio_sda = <&i2c_gpio_exp>,"gpios:4";
		i2c_exp_gpio_scl = <&i2c_gpio_exp>,"gpios:16";
		i2c_exp_gpio_delay_us = <&i2c_gpio_exp>,"i2c-gpio,delay-us:0";
		i2c_exp_bus = <&i2c_gpio_exp>, "reg:0";

		pca_addr = <&pca>,"reg:0";
	};
};

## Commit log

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2022-10-19 Added Buck and Outputs
    [buck.kicad_sch, motherboard_2022_2023.kicad_sch]
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2022-10-19 Add 2 pyro channels
    [buck.kicad_sch, motherboard_2022_2023.kicad_pcb, motherboard_2022_2023.kicad_sch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]
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2022-10-24 Added SDA/SCL & Document Titles
    [buck.kicad_sch, motherboard_2022_2023.kicad_sch, pyro_channel_pair.kicad_sch]
2022-10-24 Added Some 5V Rails and Moved PWM Extender
    [motherboard_2022_2023.kicad_pcb]
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2022-10-25 Nuked BNO055 & Re Laid Out Schematic
    [motherboard_2022_2023.kicad_sch, pyro_channel_pair.kicad_sch]
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2022-10-25 Fix pretty path
    [motherboard_2022_2023.kicad_pcb]
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2022-10-25 Fixed Logo Transparency
    [motherboard_2022_2023.kicad_pcb]
2022-10-25 Fix floods
    [motherboard_2022_2023.kicad_pcb]
2022-10-25 Progress on Routing Motherboard
    [motherboard_2022_2023.kicad_pcb, motherboard_2022_2023.kicad_sch, pyro_channel_pair.kicad_sch]
2022-10-25 Fixed Traces to PWM Out
    [motherboard_2022_2023.kicad_pcb, motherboard_2022_2023.kicad_sch, pyro_channel_pair.kicad_sch]
2022-10-25 Added Resistors to MOSFET at Ben's Request
    [motherboard_2022_2023.kicad_pcb, motherboard_2022_2023.kicad_sch, pyro_channel_pair.kicad_sch]
2022-10-27 Route rest of PCB, passes almost all meaningful DRC
    [motherboard_2022_2023.kicad_pcb, pyro_channel_pair.kicad_sch]
2022-10-27 Add 3d model for SAM-M8Q
    [SAM_AP214.STEP, motherboard_2022_2023.kicad_pcb]
2022-10-27 Add 3d model for XBee
    [XBProRPSMA.step, motherboard_2022_2023.kicad_pcb]
2022-10-27 Add 3d model for pi zero (2?) W
    [motherboard_2022_2023.kicad_pcb]
2022-10-28 Setup config.txt and modules-load.d with ansible
    [config.txt]
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2022-10-30 Impliment MPU6050 logging. Also updated various things for subscale.
    [config.txt]
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2022-11-22 Increment all IPs to fix Vagrant warning Vagrant assigns the host computer 10.82.104.1, so also assigning it to the groundstation causes a lot of issues.
2022-11-24 Added Buzzer
    [motherboard_2022_2023.kicad_pcb, motherboard_2022_2023.kicad_sch]
2022-11-24 Fixed Footprint
    [motherboard_2022_2023.kicad_pcb, motherboard_2022_2023.kicad_sch]
2022-11-25 Another Buzzer Option
    [motherboard_2022_2023.kicad_pcb, motherboard_2022_2023.kicad_sch]
2022-11-26 Add option to use standalone MPU-6050 chip Also corrects a couple small bugs in footprints
    [motherboard_2022_2023.kicad_pcb, motherboard_2022_2023.kicad_sch]
2022-11-28 Add capacitors to MPL3115 according to the datasheet
    [motherboard_2022_2023.kicad_pcb, motherboard_2022_2023.kicad_sch]
2022-11-28 Add notes to schematic
    [motherboard_2022_2023.kicad_sch]
2022-11-28 Connect XBee CTS to pi
    [motherboard_2022_2023.kicad_pcb, motherboard_2022_2023.kicad_sch]
2022-11-28 Add note to schematic
    [motherboard_2022_2023.kicad_sch]
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2022-11-29 Revert "Merge branch 'main' of https://github.com/Rose-Rocketry/NASA-USLI-2023-Electrical-Payload"
    This reverts commit 2c693e8b656697acdd5394412e94d16fb74b389e, reversing
    changes made to c3e2ab575912267e277cfde858d4ce401414edea.
    [motherboard_2022_2023.kicad_pcb, motherboard_2022_2023.kicad_sch]
2022-11-29 Revert "Rounded Corners"
    This reverts commit c3e2ab575912267e277cfde858d4ce401414edea.
    [motherboard_2022_2023.kicad_pcb]
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2022-11-29 Moved CSI to HDMI to own PCB
    [hdmi_to_csi.kicad_pcb, hdmi_to_csi.kicad_sch, motherboard_2022_2023.kicad_sch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]
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2022-11-29 Adjusted Location in Drawing
    [hdmi_to_csi.kicad_pcb]
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2022-11-29 Fix XBee CTS
    [motherboard_2022_2023.kicad_pcb, motherboard_2022_2023.kicad_sch]
2022-11-29 Remove unneeded I2C pullup resistors The pi zero 2 W already has 1.8k pullups on the board
    [motherboard_2022_2023.kicad_pcb, motherboard_2022_2023.kicad_sch]
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2022-11-30 Fixed Daughterboard
    [hdmi_to_csi.kicad_pcb, hdmi_to_csi.kicad_sch]
2022-11-30 Add XT-30 3d model
    [Amass_XT30PW-M.step, motherboard_2022_2023.kicad_pcb]
2022-11-30 Add 3d model for inductor
    [Coilcraft-XAL6030.step, motherboard_2022_2023.kicad_pcb]
2022-11-30 Add piezo 3d model
    [Piezo Buzzer.step, motherboard_2022_2023.kicad_pcb]
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2022-12-05 More robust XBee configuration (WIP)
    [config.txt]
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2022-12-05 Added Images to Title Blocks
    [buck.kicad_sch, hdmi.kicad_sch, pyro_channel_pair.kicad_sch]
2022-12-05 Switch XT-30 connector for a more common type
    [motherboard_2022_2023.kicad_pcb]
2022-12-05 Update 3d model for new connector
    [XT30U-M.step, motherboard_2022_2023.kicad_pcb]
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2022-12-06 Removed Vestigial IMU & Added Input Breakout
    [buck.kicad_sch, hdmi.kicad_sch, motherboard_2022_2023.kicad_pcb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]
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2022-12-06 Add STEMMA QT Connector
    [buck.kicad_sch, hdmi.kicad_sch, motherboard_2022_2023.kicad_pcb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]
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2022-12-06 Fixed Image
    [motherboard_2022_2023.kicad_pcb]
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2022-12-08 Add sensor logging and fix gpsd
    [__main__.py]
2022-12-13 Added SDR mount CAD
    [Housing.SLDPRT, Housing.STL]
2022-12-14 Created Step File for HDMI to CSI
    [hdmi_to_csi.step]
2022-12-30 Added Motherboard and HDMI_to_CSI board steps
    [hdmi_to_csi.step]
2023-01-14 Update config for full-scale payload
    [config.txt]
2023-01-16 Update system config for motherboard
    [config.txt]
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2023-01-17 Add buzzer boot and shutdown sounds
    [__main__.py]
2023-01-19 Fix SDA/SCL swapped on MPU6050 and MPL3115
    [motherboard_2022_2023.kicad_pcb, motherboard_2022_2023.kicad_sch]
2023-01-19 Fix flipped FFC connector
    [hdmi.kicad_sch, motherboard_2022_2023.kicad_pcb]
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2023-01-19 Use correct footprint for screw terminals
    [motherboard_2022_2023.kicad_pcb, motherboard_2022_2023.kicad_sch, pyro_channel_pair.kicad_sch]
2023-01-19 Correct resistor value
    [motherboard_2022_2023.kicad_pcb, motherboard_2022_2023.kicad_sch]
2023-01-19 Update servo connector footprints
    [motherboard_2022_2023.kicad_pcb, motherboard_2022_2023.kicad_sch]
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2023-01-19 Add JLCPCB order number placeholder
    [motherboard_2022_2023.kicad_pcb]
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2023-01-20 Start adding selectable i2c bus to board
    [motherboard_2022_2023.kicad_pcb, motherboard_2022_2023.kicad_sch]
2023-01-20 Lots of adjustments, 3 way I2C bus selection, SMD diodes
    [motherboard_2022_2023.kicad_pcb, motherboard_2022_2023.kicad_sch, pyro_channel_pair.kicad_sch]
2023-01-20 Add jumper to select pyro voltage
    [motherboard_2022_2023.kicad_pcb, motherboard_2022_2023.kicad_sch]
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2023-01-24 Revert "Change button footprint"
    This reverts commit 62573433dc6a31f4ca51f9e5dc16294e81f44105.
    [buck.kicad_sch, motherboard_2022_2023.kicad_pcb, motherboard_2022_2023.kicad_sch]
2023-01-25 Updated Version & Title Block
    [motherboard_2022_2023.kicad_pcb]
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2023-01-28 Connect XBee to SPI bus
    [motherboard_2022_2023.kicad_pcb, motherboard_2022_2023.kicad_sch]
2023-01-28 Use pour for 5V bus, fixing all valid DRC errors
    [motherboard_2022_2023.kicad_pcb]
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2023-01-29 Disconnect XBee from SPI bus (no longer needed)
    [motherboard_2022_2023.kicad_pcb, motherboard_2022_2023.kicad_sch]
2023-01-30 Tune differential pair lengths
    [motherboard_2022_2023.kicad_pcb]
2023-01-30 Added RGB Indicator LED and Potential Candidates
    [motherboard_2022_2023.kicad_pcb, motherboard_2022_2023.kicad_sch]
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2023-01-30 Traced New RGB LED
    [motherboard_2022_2023.kicad_pcb, motherboard_2022_2023.kicad_sch]
2023-01-30 Trace Fixed
    [motherboard_2022_2023.kicad_pcb]
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2023-01-31 Add holes in solder mask for alignment
    [motherboard_2022_2023.kicad_pcb]
2023-02-08 Fixed LED
    [buck.kicad_sch, motherboard_2022_2023.kicad_sch]
2023-02-15 Various updates for new PCB revision
    [config.txt]
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2023-02-17 Get all sensors up-to-date with the new board and protocol
    [config.txt]
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2023-02-20 Reduce meta packets to qos=0. qos=1 seems to cause some issues with RSMB when the groundstation side reboots...
2023-02-21 Adjust i2c config for new cable
    [config.txt]
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2023-03-19 Added Notes on PCB
    [motherboard_2022_2023.kicad_pcb, motherboard_2022_2023.kicad_sch]
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2023-03-26 Reverse door servos
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2023-10-31 Heirarchal Sheets Pin Directions Assigned
    [buck.kicad_sch, hdmi.kicad_sch, motherboard_2022_2023.kicad_sch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]
